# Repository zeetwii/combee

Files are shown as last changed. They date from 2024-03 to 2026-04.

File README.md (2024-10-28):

# Combee

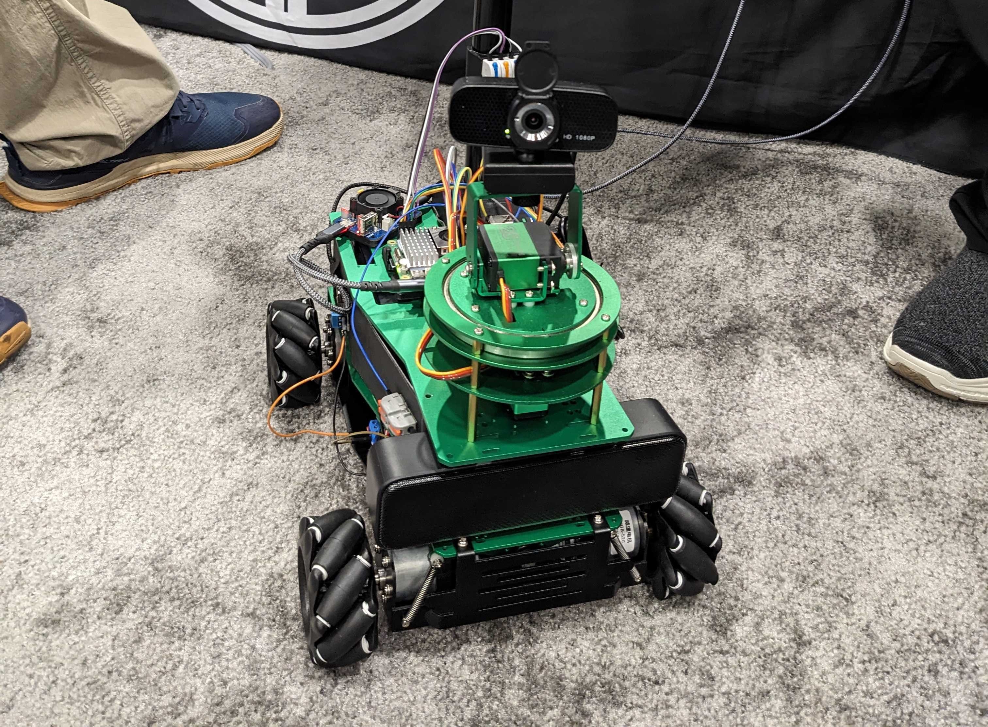
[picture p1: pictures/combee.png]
combee


Combee is a proof of concept framework for safely integrating Large Language Models (LLMs) into physical systems.  It's also a fun little robot you can talk to, and yes it is named after the pokemon.  

It's designed to show how you can securely use multiple AI models together to add multimodal capabilities to otherwise dumb systems.  If you want to build your own, check out [the build guide here](./buildGuide.md).  

## Background and Terms

In AI terms, a modal model is a model that is able to process a single type of data.  The classic example of this is a computer vision model, like YOLO.  These models can process images and videos, and do things like object recognition, but they can only process visual data, nothing else.  Thus, a multimodal model is a model that can process and respond to multiple types of data.  One of the most well known multimodal is OpenAIs ChatGPT 4.o models, which are combined text and vision models.  

Hallucinations are a thing that all generative AI models do, it's the short hand name for any and all unwanted creativity from the system.  Because LLMs and other generative AI systems can be simplified down as probability engines, they don't have any concept of truth or correctness.  This can be seen in examples like you ask an LLM to write a poem about birds, but the one it generates is for bees.  

You would be forgiven for thinking that if you have a model that can process all the data sets you want to use at once, that it must be the best model to use.  And it is by far the simplest and most optimized from a design perspective, just make the multimodal model the core of your program, pass everything to it, and let it figure things out on its own.  However this simple design has a major problem: If any part of the model hallucinates or messes up for any reason, you have no easy way to detect, contain, or fix this since the problem is literally at the core of your program.  

An alterative design is to do a multi-model design, where you have multiple individual AI models that each do their own thing independently of each other, but are able to pass data back and forth.  These multi-model systems are much more complicated to design, but since each model is stand  alone, you can check the input and data going in and out of each one, allowing you to detect and react to hallucinations and other unwanted creativity.  

This is all a lot of text, so lets use a flow diagram to visualize what we are talking about.  Lets assume you have a physical system, maybe a robot of some kind.  This system has two sensors on it, one of which changes values based on the status of the control surfaces of the system, while the other is completely independent.  We're going to make two versions of adding an AI to this system.  One with a multimodal model, and one with a multi-model implementation.  Lets look at what these look like:

| Multimodal vs Multi-Model |
| --- |
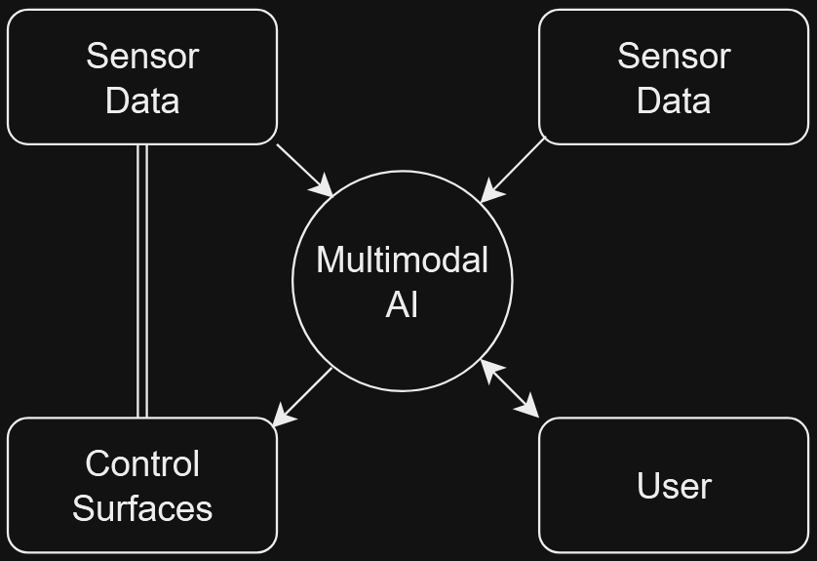
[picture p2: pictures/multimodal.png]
True multimodal solution
|  |
| This is what the solution looks like when tying everything directly to a multimodal AI.  You can see it's very simple and optimized from a design perspective.  However if and when the AI does something you don't want, your very limited in both becoming aware of the problem or reacting to it, since if the multimodal AI goes bad, there's no real way for the system to become aware of this.  |
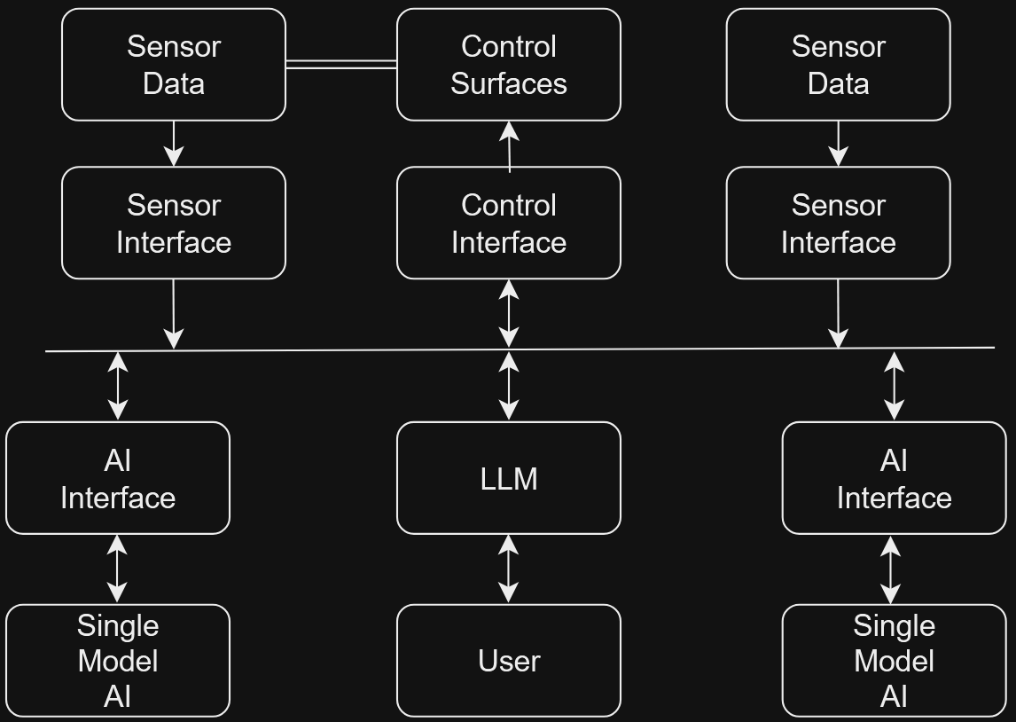
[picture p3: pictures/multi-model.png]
Mult-Model solution
|  |
| This is the same system, but using several standalone AI models to mimic a single multimodal one.  Notice how none of the AIs connect to any of the systems directly, they're all going through an interface of some kind for each sensor and system, including each other.  These interfaces are acting as API calls for the underlying sensor or system.  This has the advantage of black boxing each of the AIs, allowing you to change them out without having to retrain the system.  Additionally it means that you can detect things like hallucinations by using the same methods you would use for any normal input validation from a user.  This method has a lot of long term advantages for the system, but as the image shows is far more complicated to initially code.  |

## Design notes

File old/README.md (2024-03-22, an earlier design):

# Combee

Combee is a proof of concept framework for safely integrating Large Language Models (LLMs) into physical systems.  It's also a fun little robot you can talk to, and yes it is named after the pokemon.  

**Table of Contents**
- [Background](#background)
- [Framework Description](#framework-description)
- [Installation and Use](#installation-and-usage)

## Background

Human controlled robotics, and indeed human controlled physical systems in general have always struggled when it comes to how are they actually controlled.  Your controller ends up being the language that the operator uses to communicate with your machine, with things like button presses and joystick movements acting like words and sentences.  There are two glaring issues with this: first this is a language the operator needs to learn since humans communicate with words and not joysticks, and second that the more complex the interactions you wish to allow between machine and operator, the more complex of a controller you must design.  

LLMs present an elegant solution to these two problems.  By using an LLM as an human-machine interface the human operator is able to interact and communicate to the machine in their natural language, no training or tutorials required.  At the same time, human languages are very good at conveying both complex and simple topics.  So if the operator wants the robot to do a funny dance, they can just say "Do a funny dance", if they want it to move forward X meters and turn Y degrees, they can again just tell it so, without requiring a new interface or special steps.  

This isn't to say that LLMs are perfect in this role.  Any generative AI system is going to be vulnerable to hallucinations, or generating unwanted or invalid data from user input.  This problem becomes worse when you look at multimodal systems, where the generative AI model is performing multiple tasks such as vision recognition and text analysis, because it quickly becomes impossible to both tell what part of the system created the hallucination, and what is a hallucination versus normal input.  To confront this problem, Combee is a multi-model framework, where you the engineer are able to separate and bind different generative AI models so that you can still use these systems as an interface, but are able to limit the ability of false or bad data from them to affect the rest of the system.  

## Framework Description

The combee framework is a multi-model framework that allows multiple AI models to interface and communicate with physical sensors in an abstracted manner without the need for retraining.  In english, this means we created a framework where you the user can plug in any LLM or other model of your choosing and have that model instantly begin interpreting and interfacing with other connected systems and sensors in a secure way via a user controlled API.  It sounds complicated, but it will make sense once we break it down.  

### Multimodal vs Multi-Model

The first unique part of this framework is that we support a multi-model environment instead of a multimodal one.  Multimodal models are AI models that are designed to process and interpret multiple types of the data at the same time, such as text and video.  They are very simple to implement, since you only need to call one model for everything, but can get very large in size, and difficult to analyze if something goes wrong, since its hard to tell what part of the model is causing the problem.  Multi-model systems are systems where multiple independent AI models are sharing data with each other.  These systems are more complicated to implement than a multimodal one, but allow for the isolation of individual models, so that an error in one can stop before affecting the other.  Additionally because each model is only doing a single task, smaller more light-weight models can be used, which makes for easier deployment on hardware like Raspberry Pis.  

### API Abstraction

The second big part of the framework is having each of the models interact with the other sensors and systems via API.  This does two main things: First it allows multiple models to communicate and listen to the same sensor or system, and two it allows hallucination problems to become bounded into more general invalid input problems.  This is because rather than checking if the open-ended question of did the model generate what the user wanted correctly, we instead just have to check and validate if the model generated the API call correctly.  In other words, we are turn what would normally be an open ended write your own answer question into a multiple choice one.  

## Installation and Usage

To install, just run: 

```bash
pip install -r requirements.txt
```

This will install all the python dependencies for the project.  

### System Usage

Combee works by the user defining and describing all the sensors and systems the LLM will be connected to in a YAML file.  These descriptions should be in plain human understandable text, and will be passed to the LLM as a part of it's initial context for every question the user asks.  This will then be paired up with the output from those sensors and passed in as the full context for each question from the user.  

Eventually we will be moving over to a two tiered approach, where the LLM is first given the static description of all sensors and systems, and asked which data sets it wants to retrieve to answer the question, and then a second time with that data from the sensor.  By separating it out and only pulling what data you need, we hope to be able to better reduce the size of the context when and if the user asks about historical data.  However, because we currently use message queues as our integration method, the system is only able to see live data and nothing historical, thus this change will be added when we switch to a more database like backend.  

The robot in its current form is voice controlled, where the user pushes and holds the button on its head to record the audio that represents their request.  When they release the button the wav file is passed to OpenAI's Whisper API to transcribe from audio to text.  It is possible to run this locally, but because our example hardware is a Raspberry Pi 4, we use the cloud version for the faster response time.

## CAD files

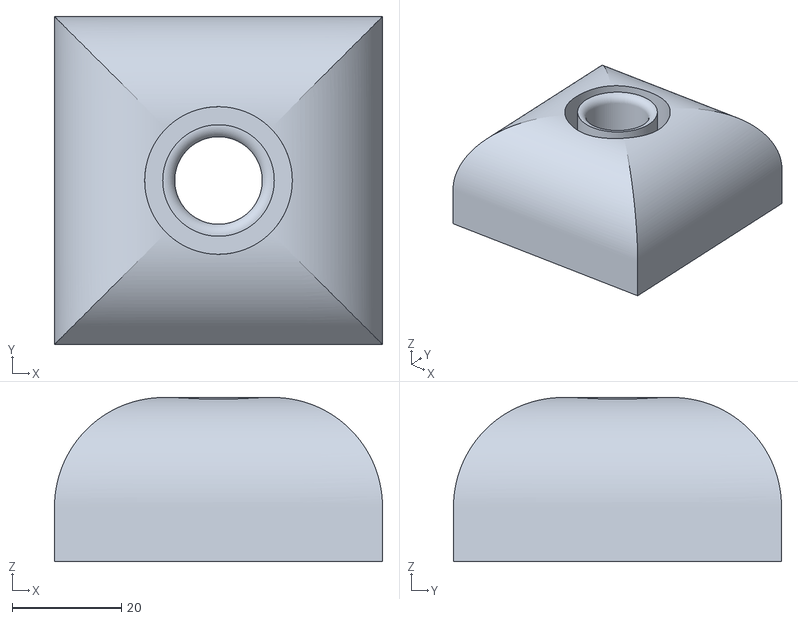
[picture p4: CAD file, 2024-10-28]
3dFiles/combeeBaseSquare.stl
60.0 x 60.0 x 30.0

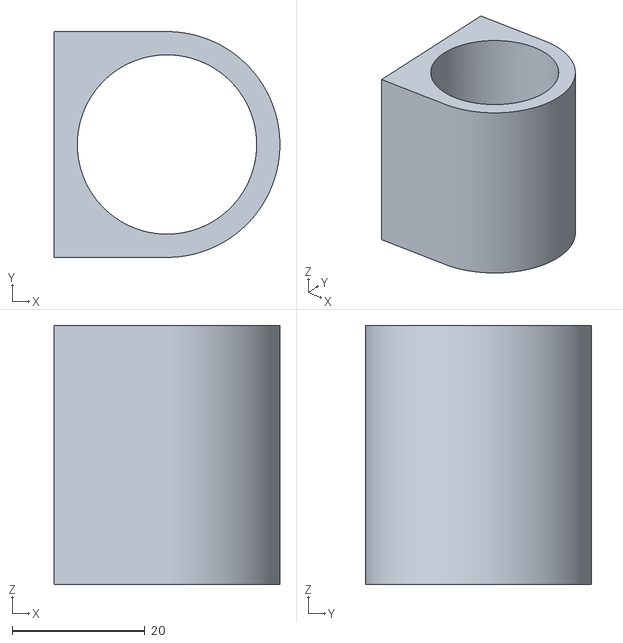
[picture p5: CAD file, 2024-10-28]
3dFiles/combeePoleCable.stl
34.0 x 34.0 x 39.0

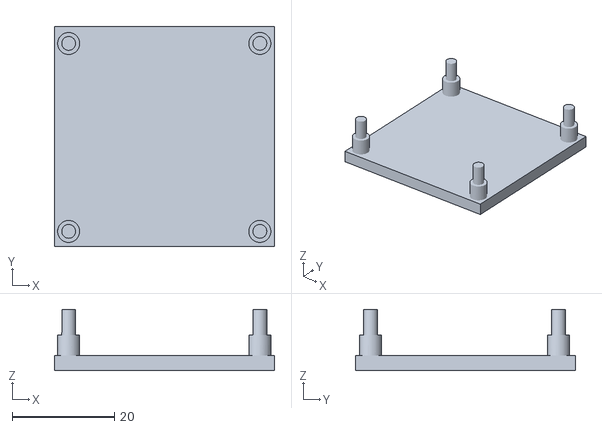
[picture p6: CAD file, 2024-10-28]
3dFiles/L298NRiser_Edited.stl
43.0 x 43.0 x 12.0

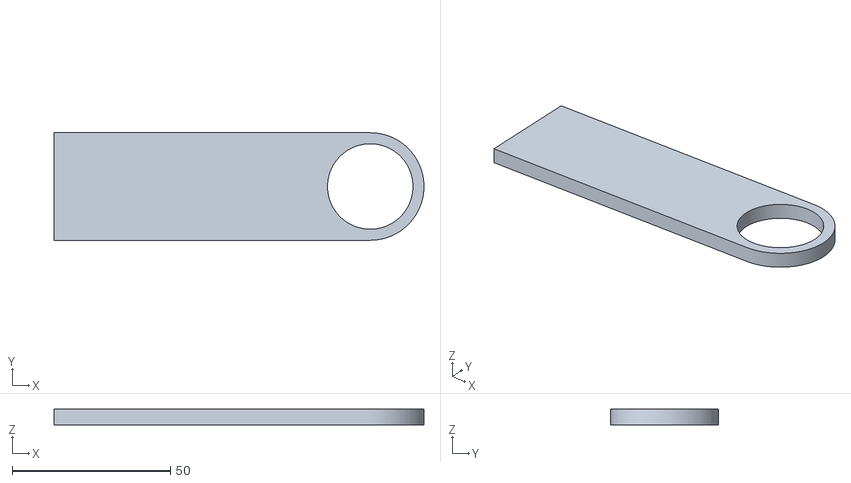
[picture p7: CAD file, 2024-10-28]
3dFiles/combeePoleMic.stl
117.0 x 34.0 x 5.00

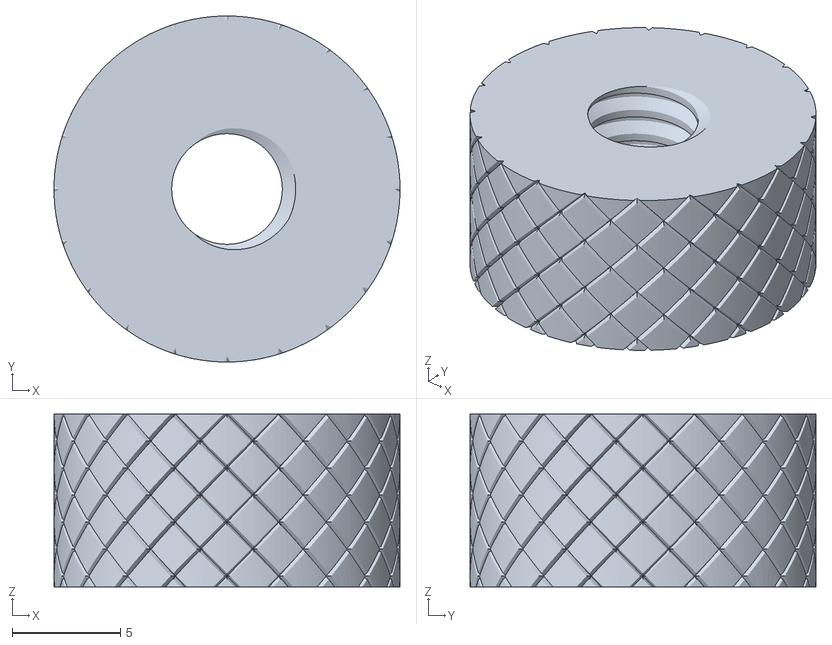
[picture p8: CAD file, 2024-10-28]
3dFiles/combeeCameraLock.stl
16.0 x 16.0 x 8.00

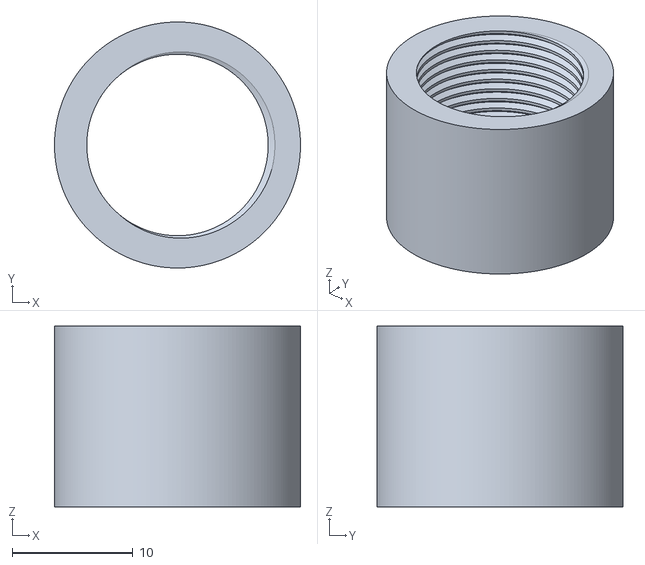
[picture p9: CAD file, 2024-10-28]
3dFiles/combeeButton.stl
20.4 x 20.4 x 15.0

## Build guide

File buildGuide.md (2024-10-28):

# Combee Build Guide

This is a quick guide for building Combee as is.  I've broken the guide up into the different subsystems to keep things easy to follow.  Everything I used to make Combee is from Amazon and similar websites, and I included links to everything.

## Parts List

Here is the breakout of all the parts and their costs when it comes to building Combee.  The total cost for everything as I built it is roughly $746 if buying off Amazon and aliexpress.  

### Computer

- [Raspberry Pi 5 - 8GB version](https://www.adafruit.com/product/5813)
  - $80 at most official resellers
- [Raspberry Pi 5 Active cooler](https://www.adafruit.com/product/5815)
  - $5 at most official resellers
  - Running any AI models on the Pi will get it very hot, so I strongly recommend some form of active cooling, and the official cooler works really well for this.  
- [5V5A PD power module](https://www.aliexpress.us/item/3256806175607588.html)
  - $14 after shipping
  - The Pi 5 will throttle itself unless it gets 5V5A directly from a power source.  This is a really weird combo from a power delivery stand point, combining the lowest voltage with the highest current supported by the spec.  As such, most battery packs do not natively support this power combination.  By using this power converter, we ensure that regardless of the battery pack being used, we're giving the pi a voltage and current level that will let it run at max speed.  
- [3d printed protective case](https://www.printables.com/model/187691-raspberry-pi-mount-for-ikea-skadis)
  - Because the chassis of Combee is metal, if you don't have some case on the bottom of the pi, you risk the system shorting out during operation.  

Total: ~$100, possibly more if you buy a case instead of printing one.  

### Frame

- [Yahboom Large Mechanum Wheel Chassis](https://www.amazon.com/gp/product/B0BR9Q58GL/)
  - $150
- [Yahboom Pan and Tilt servo kit](https://www.amazon.com/gp/product/B0BRXVFCKX/)
  - $50
- [PCA9685 servo driver](https://www.adafruit.com/product/815)
  - $15
  - There is a pre soldered version from HiLetgo on amazon if you are nervous about your solder skills.  It's [here](https://www.amazon.com/dp/B07BRS249H)
- [L298N motor drivers](https://www.amazon.com/gp/product/B07BK1QL5T/)
  - $12
  - These come in a four pack, but we only need two

Total: $227

### Power

- 2x [Anker 737 Power Bank](https://www.amazon.com/gp/product/B09VPHVT2Z/)
  - $109 each, so $218 for both
  - These give Combee around seven hours of battery life
  - Combee needs four USB C  ports for power, which is why you need two of the power banks:
    - 1x for the Pi 5 itself
    - 1x for the servo controller
    - 2x for the motor drivers
- [Short USB C cables 5 pack](https://www.amazon.com/gp/product/B0BXX2KCT2/)
  - $30
  - You need five USB C cables for Combee, so its easier just to get them as one big pack
- [USB C Power Delivery breakout boards](https://www.amazon.com/dp/B0C6KCP592)
  - $14 for a four pack
  - These are used to power the motor drivers and servo controller over USB C.  Only three are needed, but it doesn't hurt to have a spare.  
- [Terminal Block connectors](https://www.amazon.com/dp/B07CZYGQQ3)
  - $9 for a 50 pack
  - The PD breakout boards don't ship with terminal connectors, so you have to manually solder these on.  

Total: $271

### Audio and Video

  - Generic Webcam
    - ~$30
    - Any webcam with a 1/4" mounting hole will work, but I've tested two:
      - [ROCWARE camera, mic, speaker combo](https://www.amazon.com/gp/product/B09TKCNP96/)
        - This one worked well if you are wanting to cut costs, since you can use it as a speaker and microphone as well.  However everyone that I bought would eventually die after a few months, with either the mic or speaker just deciding to die.  
      - [Tewiky Webcam](https://www.amazon.com/gp/product/B08VJ25PL1/)
        - This is the one I currently used, and it has held up well.  It does also have a mic, but I find that one too weak to use in most situations.  
  - [1/4" Threaded tripod screw adapter](https://www.amazon.com/gp/product/B079BNWB6K/)
    - $7
    - These just make it easier to connect the webcam to the pan and tilt system.  You could also just use tape or something.  
  - [TONOR Conference Microphone](https://www.amazon.com/gp/product/B07GVGMW59/)
    - $24
    - Any conference microphone will work, this is just the one that I used.  
  - [USB Speaker](https://www.amazon.com/gp/product/B086JXJ1LF/)
    - $16
    - Having a dedicated speaker is needed if your in loud spaces, and this model is easy to tape to the slot in the front of the chassis to stay in place.  
  - [Momentary switch pushbutton](https://www.adafruit.com/product/560)
    - $5
    - This is just the push to talk switch.  Could technically be any momentary switch, but I think the led ring is cool.  
  - [3/4in PVC pipe](https://www.amazon.com/gp/product/B085B4Y5V6/)
    - $25 from amazon
    - $5 from a hardware store
    - This is just to give hight to the microphone and push to talk button.  You only need about two feet worth of pipe to make something thats tall enough to be easily interacted with.  

Total: $107

### Optionals

None of these are needed, but I used them in my build to make things easier to take apart and disassemble / repair.  

  - [Gorilla Tape](https://www.amazon.com/gp/product/B082TQ3KB5/)
    - $12
    - This is great for attaching stuff quickly
  - [Dupont cables](https://www.amazon.com/gp/product/B01EV70C78/)
    - $7
    - These are technically essential, since this is the connector style the pi pins use, but you can always just crimp your own wires.  
  - [Multi to one splicing connectors](https://www.amazon.com/gp/product/B09VSF5TV2/)
    - $15
    - The two to one connectors in this kit are great for the motor drivers.  To make those work, you need to combine the ground line from the USB C breakout boards with the ground on the pi in order for the signals to be read correctly.  These are a super easy way to do that.  
  - [Inline splicing connector](https://www.amazon.com/gp/product/B0BM4B3D6T/)
    - $7
    - These are great for the push to talk button, since they can create an easy disconnect point between the pi and the cable harness for the button.  

Total: $41

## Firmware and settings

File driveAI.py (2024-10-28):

import pika # needed to read messages out via RabbitMQ
#import threading # needed for multi threads
from gpiozero import Motor # needed for motor control
import time # needed for sleep

class DriveAI:
    """
    Class that controls the motors and navigation for the rover

    Note: currently doesn't navigate
    """

    def __init__(self, maxSpeed=1):
        """
        Initialization method

        Args:
            maxSpeed (int, optional): The max speed to use for the motors, should be between 0 and 1. Defaults to 1.
        """
        
        # set up all four motors
        #self.frontLeft = Motor(forward="BOARD29", backward="BOARD31")
        #self.backLeft = Motor(forward="BOARD35", backward="BOARD37")
        self.frontLeft = Motor(forward="BOARD31", backward="BOARD29")
        self.backLeft = Motor(forward="BOARD37", backward="BOARD35")
        self.frontRight = Motor(forward="BOARD32", backward="BOARD36")
        self.backRight = Motor(forward="BOARD38", backward="BOARD40")
        
        # set speed to zero
        self.frontLeft.forward(0)
        self.backLeft.forward(0)
        self.frontRight.forward(0)
        self.backRight.forward(0)

        # fix max speed if entered wrong
        while abs(maxSpeed) > 1:
            maxSpeed = abs(maxSpeed) / 10
        
        print(f"DriveAI started, motors have a max speed of: {str(maxSpeed)}")
        self.maxSpeed = maxSpeed

        #TODO Change these to pull from a yaml config
        self.turnRate = 107.5 # turn 107.5 degrees a second
        self.moveRate = 1.1667 # move 14 in a second

        # set up RabbitMQ
        self.connection = pika.BlockingConnection(pika.ConnectionParameters(host='localhost'))
        self.channel = self.connection.channel()

        self.channel.queue_declare(queue='moveInput')
        self.channel.queue_declare(queue='audioInput')
        self.channel.basic_consume(queue='moveInput', on_message_callback=self.driveCallback, auto_ack=True)

    def startListening(self):
        """
        Starts listening to the message queues
        """

        print("Beginning RabbitMQ listener")
        self.channel.start_consuming()

    def driveCallback(self, ch, method, properties, body):
        """
        Callback method for drive input queue

        Args:
            ch (_type_): _description_
            method (_type_): _description_
            properties (_type_): _description_
            body (str): message from the user
        """
        message = body.decode()
        #print(message)

        command = str(message).split(', ')

        if command[0].startswith("TURN"):
            if len(command) == 2: # correct length
                try:
                    self.turn(float(command[1]))
                except ValueError:
                    print("Error, expected angle value could not turn into a float")
                    self.channel.basic_publish(exchange='', routing_key='audioInput', body="Error from the navigation AI, expected angle value could not turn into a float")
            else:
                print("Error, unexpected number of of commands")
                self.channel.basic_publish(exchange='', routing_key='audioInput', body="Error from the navigation AI, unexpected number of commands")
        elif command[0].startswith("MOVED"):
            if len(command) == 3:
                try:
                    self.moveD(float(command[1]), float(command[2]))
                except ValueError:
                    print("Error, expected values could not turn into a float")
                    self.channel.basic_publish(exchange='', routing_key='audioInput', body="Error from the navigation AI, expected angle value could not turn into a float")
            else:
                print("Error, unexpected number of of commands")
                self.channel.basic_publish(exchange='', routing_key='audioInput', body="Error from the navigation AI, unexpected number of commands")
        elif command[0].startswith("MOVET"):
            if len(command) == 3:
                try:
                    self.moveT(float(command[1]), float(command[2]))
                except ValueError:
                    print("Error, expected values could not turn into a float")
                    self.channel.basic_publish(exchange='', routing_key='audioInput', body="Error from the navigation AI, expected angle value could not turn into a float")
            else:
                print("Error, unexpected number of of commands")
                self.channel.basic_publish(exchange='', routing_key='audioInput', body="Error from the navigation AI, unexpected number of commands")
        else:
             print("Error, unexpected command") 
             self.channel.basic_publish(exchange='', routing_key='audioInput', body="Error from the navigation AI, unexpected commands")  


    def turn(self, angle):
        """
        Handles turn movements

        Args:
            angle (float): the angle to turn to in degrees
        """

        turnTime = abs(float(angle)) / self.turnRate # calc how long to turn

        if angle > 0: # turn right
            # Left motors forward, right motors reverse
            self.frontLeft.forward(self.maxSpeed)
            self.backLeft.forward(self.maxSpeed)
            self.frontRight.backward(self.maxSpeed)
            self.backRight.backward(self.maxSpeed)

            print(f"Turn right for {str(turnTime)} seconds")
            time.sleep(turnTime)

            # set speed to zero
            self.frontLeft.forward(0)
            self.backLeft.forward(0)
            self.frontRight.forward(0)
            self.backRight.forward(0)
        else: # turn left
            # Left motors reverse, right motors forward
            self.frontLeft.backward(self.maxSpeed)
            self.backLeft.backward(self.maxSpeed)
            self.frontRight.forward(self.maxSpeed)
            self.backRight.forward(self.maxSpeed)

            print(f"Turn left for {str(turnTime)} seconds")
            time.sleep(turnTime)
            
            # set speed to zero
            self.frontLeft.forward(0)
            self.backLeft.forward(0)
            self.frontRight.forward(0)
            self.backRight.forward(0)


    def moveD(self, angle, distance):
        """
        Handles moving a given distance

        Args:
            angle (float): the angle to move at (0 for forward, 180 for reverse, anywhere in between)
            distance (float): the distance to travel in feet
        """

        # translate distance into time
        moveTime = distance / self.moveRate

        if -90 <= float(angle) <= 90:
            self.moveForward(float(angle), moveTime)
        else:
            self.moveReverse(float(angle), moveTime)


    def moveT(self, angle, moveTime):
        """
        Handles moving a given time

        Args:
            angle (float): the angle to move at (0 for forward, 180 for reverse, anywhere in between)
            moveTime (float): the time to travel in seconds
        """

        if -90 <= float(angle) <= 90:
            self.moveForward(float(angle), moveTime)
        else:
            self.moveReverse(float(angle), moveTime)

    
    def moveReverse(self, angle, runtime):
        """
        Handles moving the robot backwards at a given angle for a given time

        Args:
            angle (float): The angle to move at
            runtime (float): the time to run
        """

        # because of mecanum wheel design all movements are done in movement pairs across the four wheels
        primary = self.maxSpeed
        secondary = self.maxSpeed

        angle = float(angle) # cast to float for math

        # check to make sure angle is within valid range:

        # check to make sure its not larger than 180 degrees
        while angle > 180:
            angle = angle - 360
        
        while angle < -180: 
            angle = angle + 360

        if -90 <= angle <= 90: # actually moving forward
            self.moveForward(angle, runtime)

        if angle > 0: # moving backwards in a right leaning angle
            # motors frontLeft and rearRight move with secondary
            # motors frontRight and rearLeft move with primary
            if angle <= 135: # secondary motors move forward
                secondary = secondary - (secondary * ((angle - 90) / 45))
                
                # catch edge cases
                if secondary > 1:
                    secondary = 1
                if secondary < 0:
                    secondary = 0
                
                # Reverse
                #frontRight = primary
                #rearLeft = primary
                self.backLeft.backward(primary)
                self.frontRight.backward(primary)

                # Forward
                #frontLeft = secondary
                #rearRight = secondary
                self.frontLeft.forward(secondary)
                self.backRight.forward(secondary)

                time.sleep(float(runtime))

                # turn all motors off
                self.frontLeft.forward(0)
                self.backLeft.forward(0)
                self.frontRight.forward(0)
                self.backRight.forward(0)

                print(f"Move Reverse, 90 to 135: P: {str(primary)} S: {str(secondary)}")

            else: # secondary motors move in reverse
                secondary = (secondary * ((angle - 135) / 45))
                
                # catch edge cases
                if secondary > 1:
                    secondary = 1
                if secondary < 0:
                    secondary = 0
                
                # Reverse
                self.frontLeft.backward(secondary)
                self.backLeft.backward(primary)
                self.frontRight.backward(primary)
                self.backRight.backward(secondary)
                
                #frontRight = primary
                #rearLeft = primary
                #frontLeft = secondary
                #rearRight = secondary

                time.sleep(float(runtime))

                # turn all motors off
                self.frontLeft.forward(0)
                self.backLeft.forward(0)
                self.frontRight.forward(0)
                self.backRight.forward(0)

                print(f"Move Reverse, 135 to 180: P: {str(primary)} S: {str(secondary)}")

        else: # moving backward in a left leaning direction
            # motors frontLeft and rearRight move with primary
            # motors frontRight and rearLeft move with secondary

            if abs(angle) <= 135: # secondary motors move forward
                secondary = secondary - (secondary * ((abs(angle) - 90) / 45))
                
                # catch edge cases
                if secondary > 1:
                    secondary = 1
                if secondary < 0:
                    secondary = 0
                
                # Forward
                #frontRight = secondary
                #rearLeft = secondary
                self.backLeft.forward(secondary)
                self.frontRight.forward(secondary)

                # Reverse
                #frontLeft = primary
                #rearRight = primary
                self.frontLeft.backward(primary)
                self.backRight.backward(primary)

                time.sleep(float(runtime))

                # turn all motors off
                self.frontLeft.forward(0)
                self.backLeft.forward(0)
                self.frontRight.forward(0)
                self.backRight.forward(0)

                print(f"Move Reverse, -90 to -135: P: {str(primary)} S: {str(secondary)}")

            else: # secondary motors move in reverse
                secondary = (secondary * ((abs(angle) - 135) / 45))
                
                # catch edge cases
                if secondary > 1:
                    secondary = 1
                if secondary < 0:
                    secondary = 0
                
                # Reverse
                #frontRight = secondary
                #rearLeft = secondary
                #frontLeft = primary
                #rearRight = primary
                self.frontLeft.backward(primary)
                self.backLeft.backward(secondary)
                self.frontRight.backward(secondary)
                self.backRight.backward(primary)

                time.sleep(float(runtime))

                # turn all motors off
                self.frontLeft.forward(0)
                self.backLeft.forward(0)
                self.frontRight.forward(0)
                self.backRight.forward(0)

                print(f"Move Reverse, -135 to -180: P: {str(primary)} S: {str(secondary)}")


    def moveForward(self, angle, runtime):
        """
        Handles moving the robot forward at a given angle for a given time

        Args:
            angle (float): The angle to move at
            runtime (float): the time to run
        """

        # because of mecanum wheel design all movements are done in movement pairs across the four wheels
        primary = self.maxSpeed
        secondary = self.maxSpeed

        angle = float(angle) # cast to float for math

        if angle >= 0: # move forward in a right leaning angle
            # motors frontLeft and rearRight move with primary
            # motors frontRight and rearLeft move with secondary
            if angle <= 45: # secondary motors moving forward
                secondary = secondary - (secondary * (angle / 45))
                # catch edge cases
                if secondary > 1:
                    secondary = 1
                if secondary < 0:
                    secondary = 0

                # all forward
                #frontLeft = primary
                #rearRight = primary
                #frontRight = secondary
                #rearLeft = secondary 
                self.frontLeft.forward(primary)
                self.backLeft.forward(secondary)
                self.frontRight.forward(secondary)
                self.backRight.forward(primary)   

                time.sleep(float(runtime))

                # turn all motors off
                self.frontLeft.forward(0)
                self.backLeft.forward(0)
                self.frontRight.forward(0)
                self.backRight.forward(0)

                print(f"Move Forward, 0 to 45: P: {str(primary)} S: {str(secondary)}")

            elif angle <= 90: # secondary motors moving in reverse
                secondary = (secondary * ((angle - 45) / 45))
                # catch edge cases
                if secondary > 1:
                    secondary = 1
                if secondary < 0:
                    secondary = 0

                # primary forward
                #frontLeft = primary
                #rearRight = primary
                self.frontLeft.forward(primary)
                self.backRight.forward(primary)

                # secondary reverse
                #frontRight = secondary
                #rearLeft = secondary
                self.backLeft.backward(secondary)
                self.frontRight.backward(secondary)

                time.sleep(float(runtime))

                # turn all motors off
                self.frontLeft.forward(0)
                self.backLeft.forward(0)
                self.frontRight.forward(0)
                self.backRight.forward(0)

                print(f"Move Forward, 45 to 90: P: {str(primary)} S: {str(secondary)}")
            else:
                # angle is greater than 90 degrees which means we're actually going in reverse
                self.moveReverse(angle, runtime)
        else: # move forward in a left leaning direction
            # motors frontRight and rearLeft move with primary
            # motors frontLeft and rearRight move with secondary
            if angle >= -45: # secondary motors moving forward
                secondary = secondary - (secondary * (abs(angle) / 45))
                # catch edge cases
                if secondary > 1:
                    secondary = 1
                if secondary < 0:
                    secondary = 0

                # all forward
                #frontRight = primary
                #rearLeft = primary
                #frontLeft = secondary
                #rearRight = secondary 
                self.frontLeft.forward(secondary)
                self.backLeft.forward(primary)
                self.frontRight.forward(primary)
                self.backRight.forward(secondary)   

                time.sleep(float(runtime))

                # turn all motors off
                self.frontLeft.forward(0)
                self.backLeft.forward(0)
                self.frontRight.forward(0)
                self.backRight.forward(0)

                #print(f"Move Forward, -0 to -45: P: {str(primary)} S: {str(secondary)}")

            elif angle >= -90: # secondary motors moving in reverse
                secondary = (secondary * ((abs(angle) - 45) / 45))
                # catch edge cases
                if secondary > 1:
                    secondary = 1
                if secondary < 0:
                    secondary = 0

                # primary forward
                #frontRight = primary
                #rearLeft = primary
                self.backLeft.forward(primary)
                self.frontRight.forward(primary)

                # secondary reverse
                #frontLeft = secondary
                #rearRight = secondary  
                self.frontLeft.backward(secondary)
                self.backRight.backward(secondary)  

                time.sleep(float(runtime))

                # turn all motors off
                self.frontLeft.forward(0)
                self.backLeft.forward(0)
                self.frontRight.forward(0)
                self.backRight.forward(0)

                print(f"Move Forward, -45 to -90: P: {str(primary)} S: {str(secondary)}")
            else:
                # angle is greater than 90 degrees which means we're actually going in reverse
                self.moveReverse(angle, runtime)





if __name__ == "__main__":
    print("Running DriveAI")

    driveAI = DriveAI(1)
    driveAI.startListening()

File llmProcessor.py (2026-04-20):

from groq import Groq
import yaml # needed for config
import pika # needed to send messages out via RabbitMQ
import time # needed for sleep


class LLMProcessor:
    """
    Class that handles sending messages to and from the LLM
    """

    def __init__(self):
        """
        Initialization method
        """

        # String that will contain all the detected objects and their positions relative to us
        self.detectedObjects = ""

        # load context settings
        with open("./configs/context.yaml", "r") as ctxfile:
            context = yaml.safe_load(ctxfile)

        with open("./configs/billing.yaml", "r") as billingfile:
            billing = yaml.safe_load(billingfile)

        self.client = Groq(api_key=billing["groq"]["API_KEY"])

        self.personality = context["llm"]["PERSONALITY"]
        self.moveDes = context["llm"]["MOVE_DESCRIPTION"]
        self.lookDes = context["llm"]["CAMERA_DESCRIPTION"]
        self.waitDes = context["llm"]["WAIT_DESCRIPTION"]
        self.textDes = context["llm"]["TEXT_DESCRIPTION"]
        self.llmDes = context["llm"]["LLM_DESCRIPTION"]


        # set up RabbitMQ
        self.connection = pika.BlockingConnection(pika.ConnectionParameters(host='localhost'))
        self.channel = self.connection.channel()

        # Declare all the queues we will listen to or use
        self.channel.queue_declare(queue='userOutput') 
        self.channel.queue_declare(queue='cameraOutput')
        self.channel.queue_declare(queue='cameraInput')
        self.channel.queue_declare(queue='audioInput')
        self.channel.queue_declare(queue='moveInput')

        messages = [
            {
                'role': 'user',
                'content': 'Say that you are ready to go.  ',
            },
            ]
        
        response = self.client.chat.completions.create(model="llama-3.3-70b-versatile", messages=messages)
        print(response.choices[0].message.content)

        self.channel.basic_consume(queue='userOutput', on_message_callback=self.userCallback, auto_ack=True)
        self.channel.basic_consume(queue='cameraOutput', on_message_callback=self.cameraCallback, auto_ack=True)

    def cameraCallback(self, ch, method, properties, body):
        """
        Callback method for object detection

        Args:
            ch (_type_): _description_
            method (_type_): _description_
            properties (_type_): _description_
            body (_type_): _description_
        """
        
        self.detectedObjects = body.decode()
        #print(self.detectedObjects)

    def userCallback(self, ch, method, properties, body):
        """
        Callback method for user input queue, passes question to LLM

        Args:
            ch (_type_): _description_
            method (_type_): _description_
            properties (_type_): _description_
            body (str): message from the user
        """
        question = body.decode()
        self.callLLM(question=question)

    def startListening(self):
        """
        Starts listening to the message queues
        """

        print("Beginning RabbitMQ listener")
        self.channel.start_consuming()

    def callLLM(self, question):
        """
        passes the given question to the LLM

        Args:
            question (str): The string representing the user question
        """
        
        movementString = ""

        print("Sending question to LLM")

        completion = self.client.chat.completions.create(
            model="llama-3.3-70b-versatile",
            messages=[
                {"role": "system", "content": f"{str(self.personality)}"},
                {"role": "system", "content": f"{str(self.moveDes)}"},
                {"role": "system", "content": f"{str(self.lookDes)}"},
                {"role": "system", "content": f"The webcam currently sees the following objects: {str(self.detectedObjects)}"},
                {"role": "system", "content": f"{str(self.waitDes)}"},
                {"role": "system", "content": f"{str(self.textDes)}"},
                #{"role": "system", "content": f"{str(self.llmDes)}"},
                {"role": "system", "content": "You may combine and chain commands together however each command must be on a new line, and only one command is allowed per line.  The command should be the only thing on the line, nothing else.  Do not respond with anything other than commands, and do not abbreviate or title the commands anything other than what has been provided in the context.  Every command must be in brackets with the command type followed by a comma and then the command content.  For example, if I wanted you to say 'hello' you would respond with: [TEXT, hello].  If I wanted you to wait for 5 seconds, you would respond with: [WAIT, 5].  If you do not understand the question or do not know how to answer the question with the provided commands, respond with [TEXT, Sorry, I don't understand the question]"},
                {"role": "system", "content": "Using this sensor data and formatting instructions, try to answer the following question from the user."},
                {"role": "user", "content": f"{str(question)}"}
            ]
        )

        output = str(completion.choices[0].message.content)
        print("")
        print(output)
        
        lines = [line.strip() for line in output.split("\n")]

        for i in range(len(lines)):
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

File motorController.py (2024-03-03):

import pika # needed to send messages out via RabbitMQ
import threading # needed for multi threads
import gpiozero # needed for motor control
import time # needed for sleep

class MotorController:
    """
    Class that controls the motors for the rover
    """

    def __init__(self, maxSpeed = 1):
        """
        Initialization method

        Args:
            maxSpeed (float): the max speed of the motors, a decimal value from zero to one
        """

        self.maxSpeed = maxSpeed
        self.movementList = []

        self.turnRate = 120.0 # turns 360 degrees in 3 seconds

        #Set up the four motors
        self.frontRight = gpiozero.Motor(11, 9)
        self.backRight = gpiozero.Motor(19, 26)
        self.frontLeft = gpiozero.Motor(12, 16)
        self.backLeft = gpiozero.Motor (21, 20)

        # zero out all speed
        self.frontLeft.forward(0)
        self.frontRight.forward(0)
        self.backLeft.forward(0)
        self.backRight.forward(0)

    def processMessage(self, message):
        """
        Processes a command message generated by the LLM and adds it to the movement list

        Args:
            message (str): The movement command
        """
        
        print("Adding message")

        self.movementList.append(message)

    def moveIt(self):
        """
        Thread that drives the rover
        """
        
        print("moveIt started")

        while True:
            # zero out all speed
            self.frontLeft.forward(0)
            self.frontRight.forward(0)
            self.backLeft.forward(0)
            self.backRight.forward(0)

            time.sleep(1)

            while len(self.movementList) > 0:
                
                print("Running movement command")

                move = str(self.movementList[0]).split()

                if len(move) != 3: # incorrect format
                    print(f"Error, {self.movementList[0]} formatted incorrectly")
                else:
                    if move[0] == "Forward":
                        try:
                            runTime = float(move[2])
                            if runTime > 10:
                                runTime = 10
                            
                            self.frontLeft.forward(self.maxSpeed)
                            self.frontRight.forward(self.maxSpeed)
                            self.backLeft.forward(self.maxSpeed)
                            self.backRight.forward(self.maxSpeed)

                            time.sleep(runTime)

                            self.frontLeft.forward(0)
                            self.frontRight.forward(0)
                            self.backLeft.forward(0)
                            self.backRight.forward(0)
                        except ValueError:
                            print("Time was not represented as a float in forward message")
                            
                    elif move[0] == "Reverse":
                        try:
                            runTime = float(move[2])
                            if runTime > 10:
                                runTime = 10
                            
                            self.frontLeft.backward(self.maxSpeed)
                            self.frontRight.backward(self.maxSpeed)
                            self.backLeft.backward(self.maxSpeed)
                            self.backRight.backward(self.maxSpeed)

                            time.sleep(runTime)

                            self.frontLeft.forward(0)
                            self.frontRight.forward(0)
                            self.backLeft.forward(0)
                            self.backRight.forward(0)
                        except ValueError:
                            print("Time was not represented as a float in backward message")

                    elif move[0] == "Turn":
                        try:
                            angle = float(move[1])

                            movementTime = abs(angle/self.turnRate)

                            if angle > 0: # Turn right
                                self.frontLeft.forward(self.maxSpeed)
                                self.frontRight.backward(self.maxSpeed)
                                self.backLeft.forward(self.maxSpeed)
                                self.backRight.backward(self.maxSpeed)
                            else: # Turn left
                                self.frontLeft.backward(self.maxSpeed)
                                self.frontRight.forward(self.maxSpeed)
                                self.backLeft.backward(self.maxSpeed)
                                self.backRight.forward(self.maxSpeed)

                            time.sleep(movementTime)

                            self.frontLeft.forward(0)
                            self.frontRight.forward(0)
                            self.backLeft.forward(0)
                            self.backRight.forward(0)

                        except ValueError:
                            print("Angle was not represented as a float in turn message")
                    else:
                        print(f"Error, {str(move[0])} unknown")
                
                self.movementList.pop(0)

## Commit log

2024-08-08 switched model
2024-08-09 fixed navigation and pan tilt
    [cameraAI.py, driveAI.py, llmProcessor.py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]
2024-10-28 added 3d files and started on the build guide
    [L298NRiser_Edited.stl, combeeBaseSquare.stl, combeeButton.stl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]
